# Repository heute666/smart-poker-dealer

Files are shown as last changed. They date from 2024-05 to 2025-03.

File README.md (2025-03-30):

# smart-poker-dealer
20250330: V2.4 BOM updated, to add details of "cardout sensor", stepper ISR improvement for more stable performance when weight load is high;
20250202: V2.3 BOM updated, to add comment and mistake correction;
20241114: V2 BOM updated; stepper gear (10 teeth) stp uploaded in "stl" folder - for custom design change acc. to different stepper shaft;

20241017: V2 is releasing - an emotional bot with more stable performance
3dprint files and schematic are up to date, code is under debuging and adding setup save, quick resume previous mode function
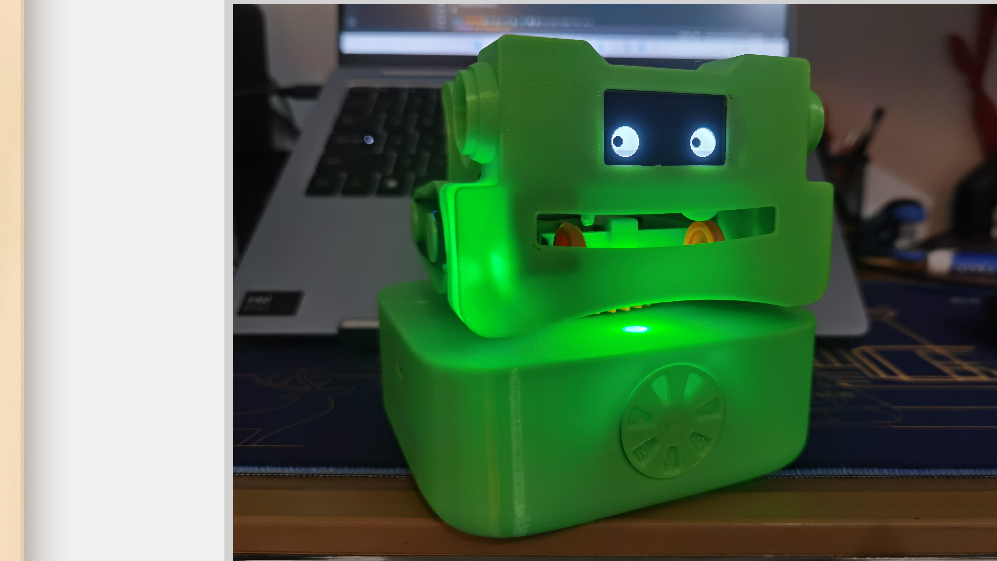
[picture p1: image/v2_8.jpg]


Initial release:
quick, light, shuffler free
3D print parts in https://www.thingiverse.com/thing:6706540;

v2 3D print, PCB updated for 1.3inch OLED, type-c charger;
PCB original files in https://oshwhub.com/heute666/pksd_indu2;

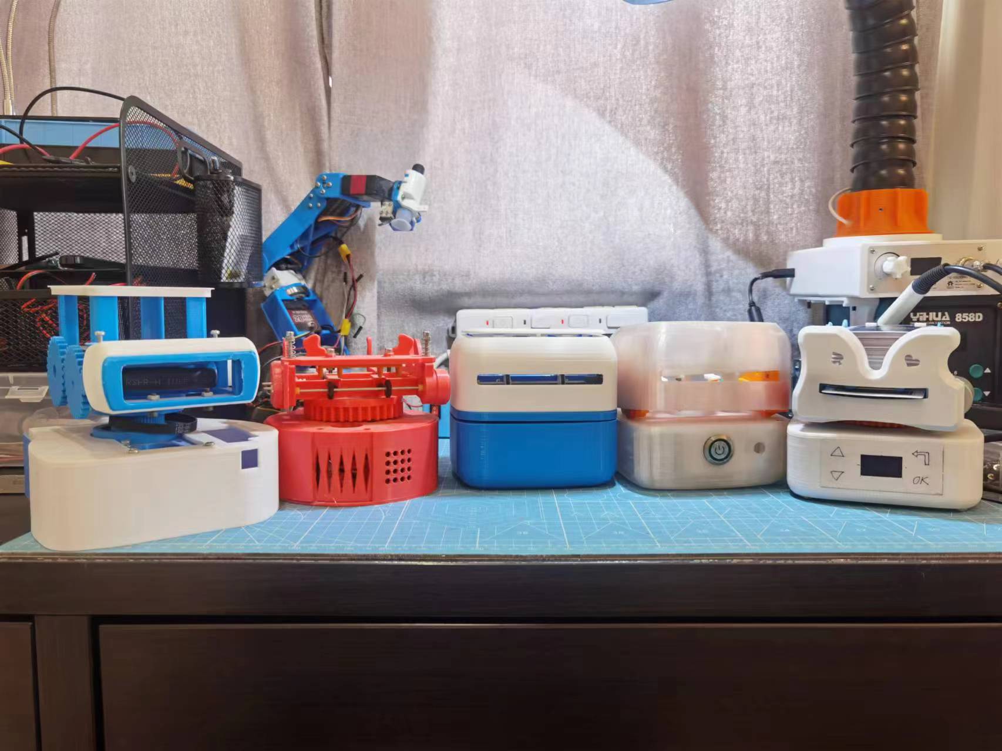
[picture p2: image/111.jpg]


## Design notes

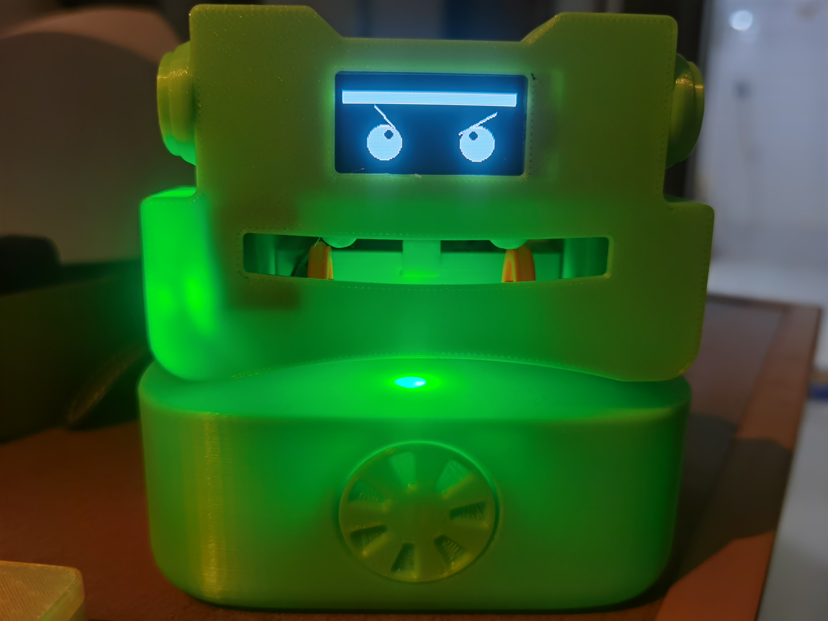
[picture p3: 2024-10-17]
image/v2_7.jpg

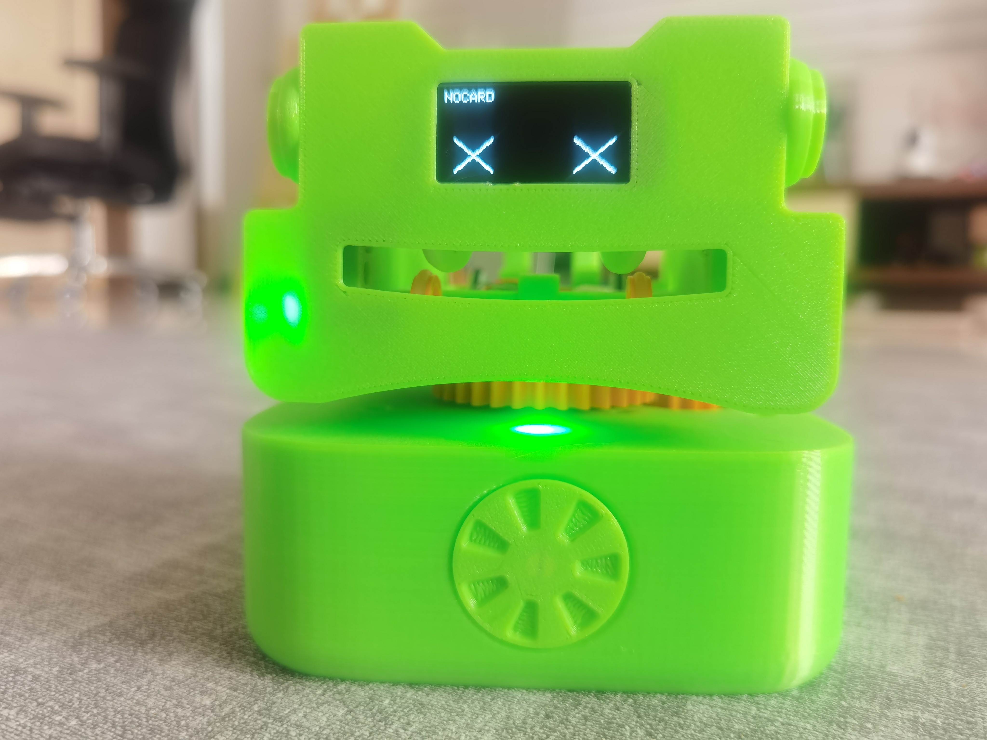
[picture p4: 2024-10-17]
image/v2_9.jpg

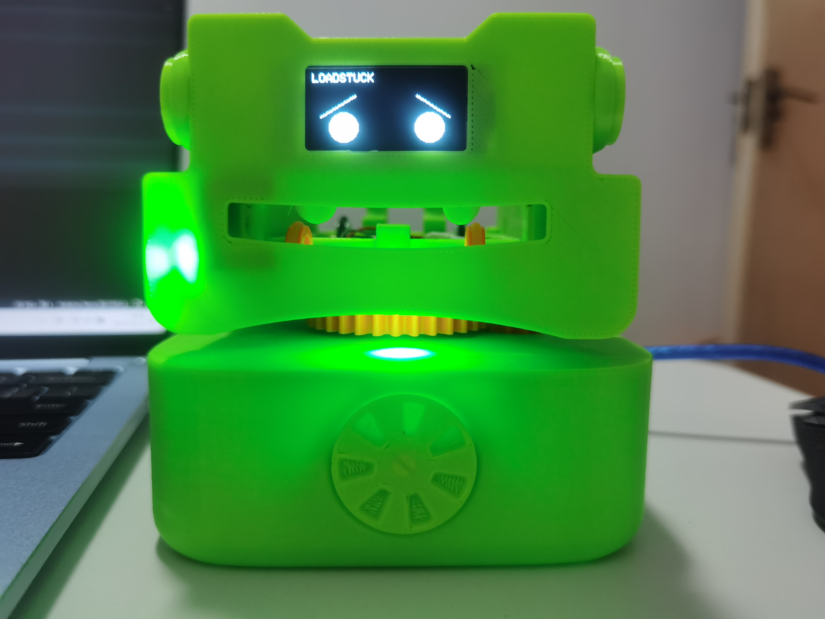
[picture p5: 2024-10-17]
image/v2_6.jpg

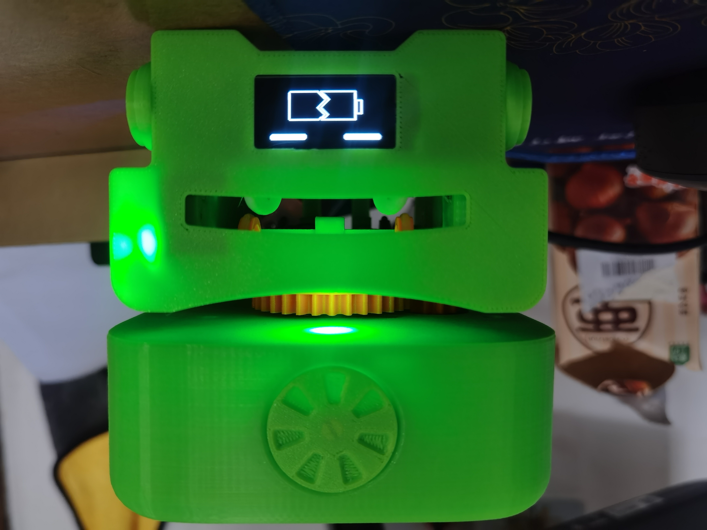
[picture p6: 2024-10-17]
image/v2_3.jpg

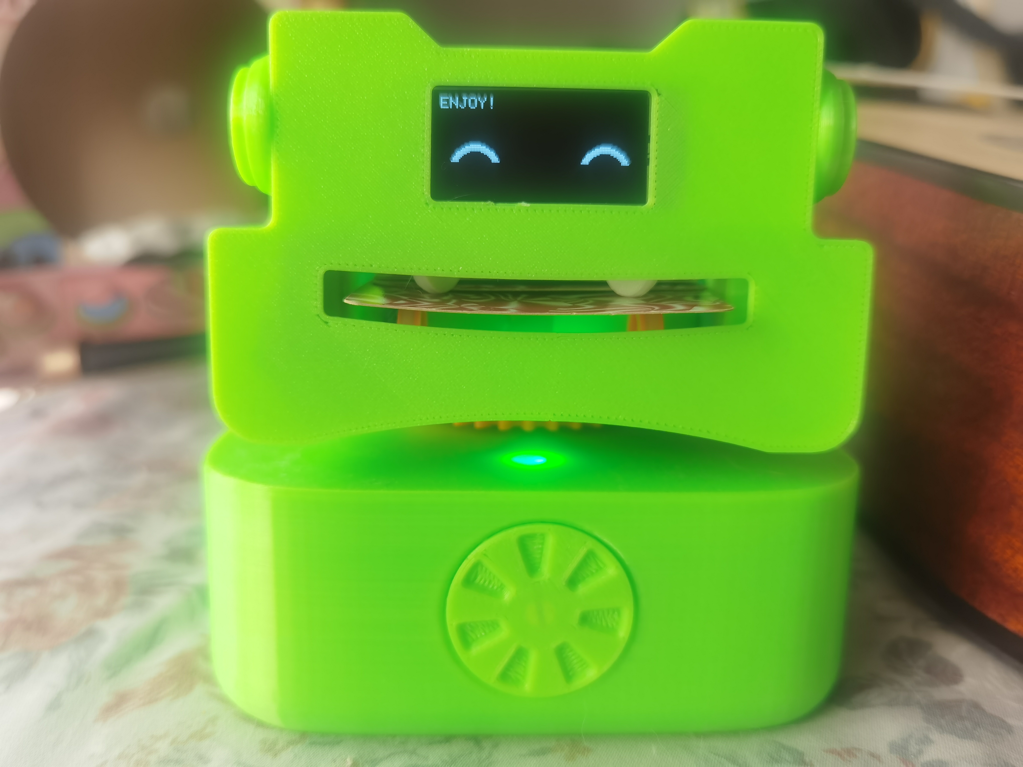
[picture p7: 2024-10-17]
image/v2_2.jpg

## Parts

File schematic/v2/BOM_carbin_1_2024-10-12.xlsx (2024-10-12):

No. | Quantity | Comment | Designator | Footprint | Value
1 | 2 | 100nf | C1,C3 | C0805 | 100nf
2 | 1 | 100uF | C2 | CAP-SMD_BD6.3-L6.6-W6.6-LS7.2-FD | 100uF
3 | 1 | NCD0805R1 | LED1 | LED0805-R-RD
4 | 1 | 330R-ori100R | R1 | R0805 | 330R-ori100R
5 | 3 | 10k | R2,R4,R5 | R0805 | 10k
6 | 1 | 20k | R3 | R0805 | 20k
7 | 1 | 1k | R6 | R0805 | 1k
8 | 1 | LM393ADR | U2 | SOIC-8_L5.0-W4.0-P1.27-LS6.0-BL
9 | 1 | ZX-PH2.0-WZ3P | U3 | CONN-TH_3P-P2.00_ZX-PH2.0-WZ3P
10 | 1 | ZX-PHB2.0-2-3PWZ | U5 | CONN-TH_6P-P2.00_ZX-PHB2.0-2-3PWZ
11 | 1 | TCRT5000 | U6 | OPTO-TH_TCRT5000
12 | 1 | WAFER-PH2.0-4PWZ | U7 | CONN-TH_4P-P2.00_WAFER-HY2.0-4PWZ

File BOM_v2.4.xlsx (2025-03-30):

 |  |  |  | https://github.com/heute666/smart-poker-dealer
L0 | L1 | L2 | L3 | L4 | 规格 | 要求 | 参考- 淘宝链接为了让大家直观知道是什么，除了备注过的，默认不代表推荐或测试过该链接实物 | 数量 | 单价 | 合计
Smart-poker-dealer |  |  |  |  |  |  |  |  |  | 135.75
 | 旋转组件
 |  | 马达侧牌仓
 |  |  | 马达侧牌仓 |  | PLA | 10齿版本- 12g 25%填充率 |  | 1 | 1.2 | 1.2
 |  |  | 直流电机总成
 |  |  |  | 直流电机 | 370 | 12V,8000-12000rpm | 淘宝链接 - 我实物是用的这种- 但超压长期运行有点容易烧 (https://item.taobao.com/item.htm?priceTId=213e36da17252054671606016e37ba&id=714138719104&ns=1&abbucket=10) | 1 | 4 | 4
 |  |  |  | 蜗杆 | 0.5M | 6-8mm长2A | 淘宝链接 (https://item.taobao.com/item.htm?id=25764808230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) | 1 | 0.08 | 0.08
 |  |  |  | 端子线 |  | PH2.0 50mm | 淘宝链接- 这里用母端 (https://item.taobao.com/item.htm?id=718353303185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) | 1 | 0.1 | 0.1
 |  |  |  | 瓷片电容 | 104 |  | 淘宝链接 (https://item.taobao.com/item.htm?priceTId=213e36da17252053488486619e37ba&id=522574858409&ns=1&abbucket=10) | 1 | 0.01 | 0.01
 |  |  | 前滚轮总成
 |  |  |  | 钢轴 | 2mm x96 | 最好95-96不会突出边界；需要用钢的，不要铁的，45或者不锈钢都行 | 淘宝链接 - 找能订做长度和倒角去毛刺的 (https://item.taobao.com/item.htm?id=563478167008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) | 1 | 0.3 | 0.3
 |  |  |  | 齿轮 | 0.5M | 10齿2A（紧配2mm轴）- 最后测下来还是10齿稳定点，需要配合10齿版本侧板用 | 淘宝链接 (https://item.taobao.com/item.htm?id=25771916651) | 1 | 0.1 | 0.1
 |  |  |  | 皮带轮 | 13mm2A |  | 淘宝链接 (https://item.taobao.com/item.htm?id=40196610656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) | 2 | 0.1 | 0.2
 |  |  |  | 硅胶圈 | 10 x 2.65 |  | 搜硅胶O型圈找对应规格 | 2 | 0.05 | 0.1
 |  |  |  | 铜轴承 | 2x4mm |  | 淘宝链接 (https://item.taobao.com/item.htm?id=534366927097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) | 2 | 0.05 | 0.1
 |  |  |  | 塑胶轴套 | 2x6mm |  | 淘宝链接 (https://item.taobao.com/item.htm?id=25735796690) | 2 | 0.02 | 0.04
 |  |  | 隔音罩 |  | TPU | 选装 |  | 1 | 0.1 | 0.1
 |  | 中间体总成
 |  |  | 牌仓传感器总成 |  |  | 可以用一个循迹传感器+特殊接线代替 |  | 1 | 2 | 2
 |  |  | 中间体 |  | PLA | 21g 25%填充率 |  | 1 | 2.1 | 2.1
 |  |  | 主轴齿轮总成
 |  |  |  | 主轴齿轮 | PLA | 12g 25%填充率 |  | 1 | 1.2 | 1.2
 |  |  |  | 螺母 | M3 |  |  | 6 | 0.02 | 0.12
 |  |  | 铜轴承 |  | 2x4mm |  | 淘宝链接 (https://item.taobao.com/item.htm?id=534366927097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) | 1 | 0.05 | 0.05
 |  |  | 螺栓 |  | M3x12 | 安装牌仓传感器 |  | 1 | 0.05 | 0.05
 |  |  | 螺栓 |  | M3x10 | 中间体连接主轴齿轮 |  | 2 | 0.05 | 0.1
 |  |  | 螺栓 |  | M2x8沉头 |  |  | 1 | 0.02 | 0.02
 |  |  | 螺母 |  | M2 |  |  | 1 | 0.02 | 0.02
 |  |  | 螺母 |  | M3 |  |  | 5 | 0.02 | 0.1
 |  | 螺栓 |  |  | M3x10 |  |  | 2 | 0.05 | 0.1
 |  | 螺母 |  |  | M3 |  |  | 2 | 0.02 | 0.04
 |  | 齿轮侧总成
 |  |  | 齿轮侧牌仓
 |  |  |  | 齿轮侧牌仓 | PLA | 15g 25%填充率 |  | 1 | 1.5 | 1.5
 |  |  |  | 螺母 | M3 |  |  | 2 | 0.02 | 0.04
 |  |  |  | 螺栓 | M2x10 |  |  | 1 | 0.02 | 0.02
 |  |  |  | 螺母 | M2 |  |  | 1 | 0.04 | 0.04
 |  |  |  | 出牌传感器总成 |  | 安装位置重要，需要PCB打板 |  | 1 | 2 | 2
 |  |  | 铜轴承 |  | 2x4mm | 几个地方需要装铜衬套当轴承的别搞错了，市面常见有2x4和2x5两种 |  | 2 | 0.05 | 0.1
 |  |  | 后滚轮总成
 |  |  |  | 同步轮 | PLA | 4g 25%填充率 |  | 4 | 0.2 | 0.8
 |  |  |  | 同步带 | MXL | 5mm宽，64齿，B64MXL |  | 1 | 0.92 | 0.92
 |  |  |  | 塑胶止挡 | 2x6mm |  |  | 1 | 0.02 | 0.02
 |  |  |  | 钢轴 | 2mm x78 | 目视无弯曲，圆柱度大约0.2？ |  | 1 | 0.3 | 0.3
 |  |  |  | 齿轮 | 0.5M | 56齿+10齿 2B |  | 1 | 0.15 | 0.15
 |  |  |  | 皮带轮 | 16mm2A |  | 淘宝链接 (https://item.taobao.com/item.htm?id=40196610656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) | 2 | 0.1 | 0.2
 |  |  |  | 氟橡胶圈 | 8.5 x 2.65 |  | 搜氟橡胶O型圈找对应规格 | 2 | 0.02 | 0.04
 |  |  | 惰齿轮
 |  |  |  | 同步轮 | PLA | 4g 25%填充率 |  | 4 | 0.2 | 0.8
 |  |  |  | 塑胶轴套 | 2x6mm |  | 淘宝链接 (https://item.taobao.com/item.htm?id=25735796690) | 1 | 0.02 | 0.02
 |  |  |  | 惰齿轮 | 0.5M | 48齿2B（单双层都可以） | 淘宝链接 (https://item.taobao.com/item.htm?id=25814212067) | 1 | 0.14 | 0.14
 |  |  |  | 惰齿轮轴 | 2mm x 10 |  | 淘宝链接 (https://item.taobao.com/item.htm?abbucket=10&id=564061088246&ns=1&priceTId=2147bf5317254444201387273e3324) | 1 | 0.04 | 0.04
 |  |  | 出牌传感器总成 |  | 如右图
 |  |  |  | PCB |  | 立创PCB文件
 |  |  |  | 电阻 | 1kΩ | 0805 |  | 1
 |  |  |  | 电阻 | 180Ω | 0805 |  | 1
 |  |  |  | 电容 | 100nf | 0805 |  | 1
 |  |  |  | LED | 自己喜欢的颜色 | 0805 |  | 1
 |  |  |  | 红外对射光耦 |  | H2010，槽宽10mm |  | 1
 |  |  |  | IC施密特发生器 |  | SN74LVC1G14DBVR SOT-23-5 |  | 1
 |  |  | 隔音罩 |  | TPU | 选装 |  | 1 | 0.1 | 0.1
 |  | 牌仓传感器PCBA |  |  |  | 制板文件和BOM，细节参阅嘉立创 | https://oshwhub.com/heute666/yi-zhi-fa-pai-ji-v1-2?code=AC-31fde32b48924dc4893be1ffcc96a859#5
 |  | 齿轮 |  |  | 0.5M | 10齿2A | 淘宝链接 (https://item.taobao.com/item.htm?id=25771916651) | 1 | 0.1 | 0.1
 |  | 铜轴承 |  |  | 2x4mm |  | 淘宝链接 (https://item.taobao.com/item.htm?id=534366927097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) | 1 | 0.05 | 0.05
 |  | 螺栓 |  |  | M3x10 |  |  | 2 | 0.05 | 0.1
 |  | 前牌仓总成
 |  |  | 出牌挡板 |  | PLA | 1g 25%填充率 |  | 2 | 0.2 | 0.4
 |  |  | 两侧装饰板 |  | PLA | 1g 25%填充率 |  | 2 | 0.2 | 0.4
 |  |  | 前牌仓 |  | PLA | 17g 25%填充率 |  | 1 | 1.7 | 1.7
 |  |  | OLED |  | 1.3寸OLED | 竖屏，SH1107驱动 |  | 1 | 13 | 13
 |  |  | 螺栓 |  | M3x8 |  |  | 2 | 0.05 | 0.1
 |  |  | 螺母 |  | M3 |  |  | 2 | 0.02 | 0.04
 |  | 后挡板 |  |  | PLA | 2g 25%填充率 |  | 2 | 0.4 | 0.8
 |  | 螺栓 |  |  | M3x8 |  |  | 2 | 0.05 | 0.1
 |  | 装饰板 |  |  | PLA | 4g 25%填充率 |  | 1 | 0.4 | 0.4
 | 底座组件
 |  | 底座总成_OP2
 |  |  | 底座总成_OP1
 |  |  |  | 轴承 | 6805 | 25mm内径，37mm外径，高7 | 淘宝链接 (https://item.taobao.com/item.htm?id=520059144981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) | 1 | 2 | 2
 |  |  |  | 底座 | PLA | 82g |  | 82 | 0.2 | 16.4
 |  |  |  | 螺母 | M3 |  |  | 2 | 0.02 | 0.04
 |  |  |  | 防滑垫 |  | 硅胶垫直径8mm-10mm都行，厚度1-2mm |  | 4 | 0.05 | 0.2
 |  |  |  | 编码器支架 | PLA | 3g |  | 3 | 0.2 | 0.6
 |  |  |  | 编码器 |  | EC11, 花轴，轴长15，5脚 |  | 1 | 1.5 | 1.5
 |  |  |  | 旋转按钮 | PLA | 3g |  | 3 | 0.2 | 0.6
 |  |  | 步进电机总成
 |  |  |  | 步进电机 | 42-34 | 常规力矩，5mm直径, 13mm长 D字短轴；短轴的不太好找，一般都是20-25mm, 太长了 | 美培亚有些二手电机轴在13-15mm之间，搜“42步进 美培亚 高34”会有些，轴径3-5的圆轴D轴都有，得改图，我把STEP放上来 | 1 | 15 | 15
 |  |  |  | 步进电机齿轮 | PLA | 1M10T, 2g |  | 1 | 0.2 | 0.2
 |  |  |  | 连接端子线 |  | PH2.0 6pin + 24AWG +XH2.54 4pin |  | 1 | 0.1 | 0.1
 |  |  | 螺栓 |  | M3X10 | 沉头，带减震垫用，固定步进电机 |  | 4 | 0.05 | 0.2
 |  |  | 螺栓 |  | M3X8 | 沉头，不带减震垫用，固定步进电机 |  | 4 |  | 0
 |  |  | 主控PCB总成
 |  |  |  | 主控PCB |  | 立创上是配v2壳体的版本 | https://u.lceda.cn/account/user/projects/index/detail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 | 1 | 15 | 15
 |  |  |  | 步进电机驱动 | TMC2208 | 也可用TMC2225 |  | 1 | 10 | 10
 | v1 |  | 屏幕及触摸模块
 | v1 |  |  | OLED屏 | 0.96 I2C | 配V1壳 |  | 1 | 10
 | v1 |  |  | OLED屏 | 1.3 I2C | 配V2壳
 | v1 |  |  | 触摸模块PCB |  | 立创上是配v2壳体的版本 | https://u.lceda.cn/account/user/projects/index/detail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 | 1 | 4
 | v1 |  |  | 端子线 |  | X2.54 8pin |  | 1 | 0.2
 | v1 |  |  | 热熔胶
 | v1 |  |  | 导电胶带 |  | 可靠性不好，将改成导电线直接埋进外壳
 | v1 |  | 铜柱 |  |  | M3, 10mm高，一边公一边母 |  | 2 | 0.3
 |  |  | 导电环支架 | v2 | PLA | 7g |  | 7 | 0.2 | 1.4
 |  |  | 电池盒 |  |  | 18650，2节串联 |  | 1 | 1 | 1
 |  |  | 螺栓 |  | M3X8 | 沉头，固定导电环支架和电池盒 |  | 5 | 0.05 | 0.25
 |  |  | 螺母 |  | M3 | 固定导电环支架和电池盒 |  | 5 | 0.02 | 0.1
 | 导电环 |  |  |  | 2A8路 | 尺寸不超过22mm直径26高,可多几路，要求并不高，咸鱼上的就可以 | 以前挺多库存件几块钱的，现在好难找，这家12路2A，塑料22mm直径，19mm长的应该可以，30块 (https://detail.tmall.com/item.htm?id=559037397190&skuId=3646480359811) | 1 | 20 | 20
 | 主轴齿轮固定片 |  |  |  | PLA | 3g |  | 1 | 0.3 | 0.3
 | 螺栓 |  |  |  | M3x8 | 固定主轴齿轮 |  | 3 | 0.05 | 0.15
 | 螺母 |  |  |  | M3 | 固定主轴齿轮 |  | 3 | 0.02 | 0.06
 | 电池 |  |  |  | 18650 | 1600mA-2000mA的就可以，动力电池更好，5C |  | 2 | 7 | 14

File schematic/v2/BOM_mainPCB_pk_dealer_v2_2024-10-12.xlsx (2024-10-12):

No. | Quantity | Comment | Designator | Footprint | Value
1 | 1 | 0.22uf | C1 | C0805
2 | 3 | 100uF | C2,C3,C39 | CAP-SMD_BD6.3-L6.6-W6.6-FD | 100uF
3 | 1 | 0.1uf | C4 | C0805
4 | 6 | 22uf | C5,C7,C27,C28,C33,C34 | C0805
5 | 3 | 100n | C6,C15,C16 | C0805
6 | 1 | 220uF | C14 | CAP-TH_BD8.0-P3.50-D0.6-FD | 220uF
7 | 1 | 4.7uF | C17 | CAP-SMD_L3.2-W1.6-FD | 4.7uF
8 | 2 | 22p | C25,C26 | C0805
9 | 4 | 10uf | C29,C31,C35,C36 | C0805
10 | 3 | 100nf | C30,C37,C38 | C0805
11 | 2 | SS54A | D2,D3 | SMA_L4.2-W2.6-LS5.1-RD
12 | 1 | MM1Z5V1 | D7 | SOD-123_L2.7-W1.6-LS3.7-RD
13 | 1 | SS54 | D8 | SMA_L4.3-W2.6-LS5.0-FD
14 | 1 | ICSP-6 | ISP | ICSP-6
15 | 1 | HC-PHD-2*3AW | J1 | CONN-TH_6P-P2.00_HCTL_HC-PHD
16 | 1 | HC-PHD-2*3A | J2 | CONN-TH_6P-P2.00_HCTL_HC-PHD-2X3A
17 | 2 | 4.7uH | L1,L2 | IND-SMD_L7.0-W6.6_0630CDMCCDS
18 | 1 | 2.2uH | L3 | IND-SMD_L7.0-W6.6_0630CDMCCDS
19 | 1 | 0.25R | R1 | R0805
20 | 1 | 100kΩ | R2 | RES-ADJ-SMD_VG039NCH
21 | 4 | 100K | R3,R4,R7,R8 | R0805
22 | 3 | 10K | R5,R6,R13 | R0805
23 | 3 | 1K | R9,R18,R29 | R0805
24 | 2 | optional | R12,R16 | R0402 | optional
25 | 2 | 51K | R17,R20 | R0805
26 | 1 | 75K | R19 | R0805
27 | 1 | 0.5R | R21 | R0805
28 | 3 | 5.1k | R22,R30,R31 | R0805
29 | 1 | 100R | R23 | R1206
30 | 1 | TMC2208模块 | U2 | TMC2208
31 | 1 | XH2.54-LI-4P | U3 | CONN-TH_4P-P2.54-XH2.54-LI-4P
32 | 2 | SX1308 | U4,U5 | SOT-23-6_L2.9-W1.6-P0.95-LS2.8-BR
33 | 1 | BLE | U6 | HDR-TH_4P-P2.54-V-M
34 | 1 | DRV8870DDA | U7 | SOPOWERPAD-8_L4.9-W3.9-P1.27-LS6.0-BL-EP
35 | 1 | ATMEGA328P-AU | U8 | TQFP-32_L7.0-W7.0-P0.80-LS9.0-BL
36 | 1 | XH2.54-LI-2P_C2922484 | U13 | CONN-TH_XH-2AW_C2908611
37 | 1 | AMS1117-5.0 | U17 | SOT-223_L6.7-W3.5-P2.30-BR
38 | 1 | IP2326 | U18 | VQFN-24_L4.0-W4.0-P0.50-BL-EP2.5
39 | 1 | BAT_CON | U19 | CONN-TH_3P-P2.54_2501S-3P
40 | 1 | SWI | U20 | SW-TH_SHOU-HAN_SS12D10G4
41 | 1 | TJ-L5FPTXHMCSLCRGB-A5 | U22 | LED-TH_4P-BD5.8-P1.30
42 | 1 | TYPE-C16PIN | USB6 | USB-C-SMD_TYPE-C16PIN
43 | 1 | 16MHz | X2 | QS

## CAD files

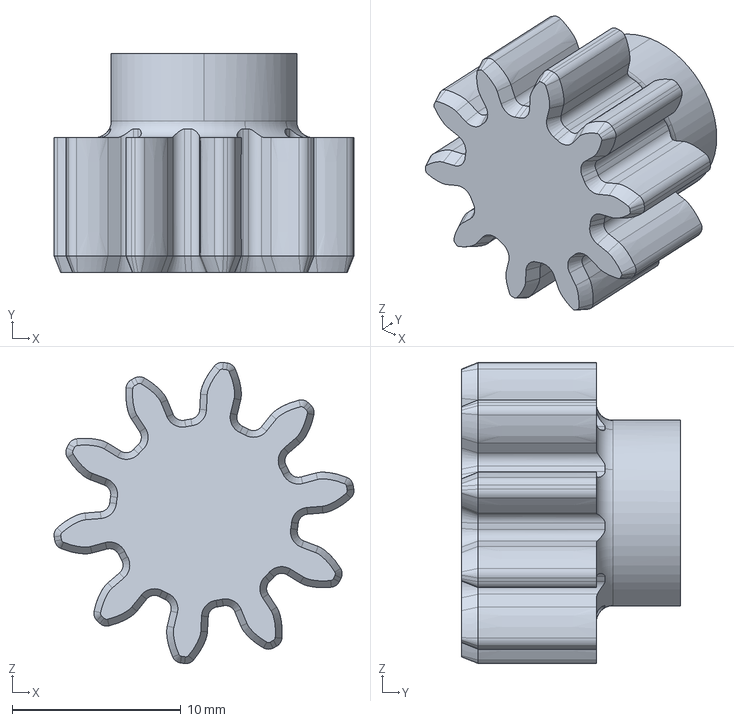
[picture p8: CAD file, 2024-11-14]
3dprint/gear_10t.stp
17.8 x 13.0 x 17.9 mm

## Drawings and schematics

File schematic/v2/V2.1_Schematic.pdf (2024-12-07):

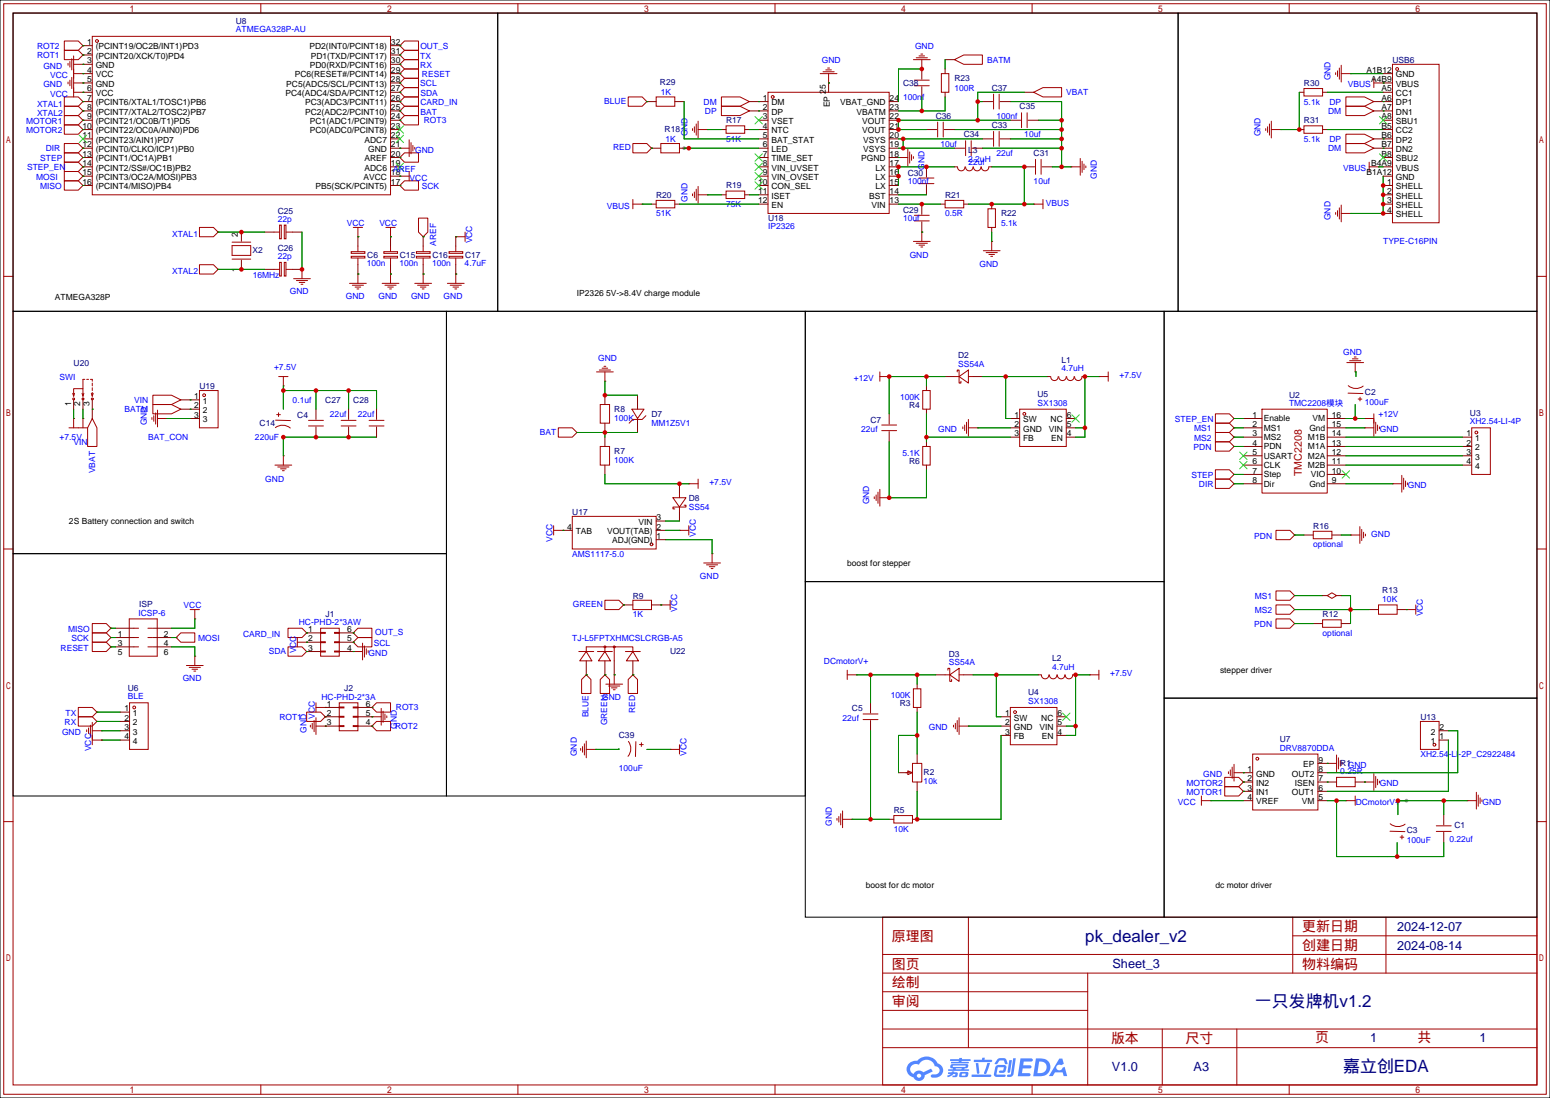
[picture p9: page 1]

C33
C34 | 10uf
10uf

2S Battery connection and switch

boost for dc motor

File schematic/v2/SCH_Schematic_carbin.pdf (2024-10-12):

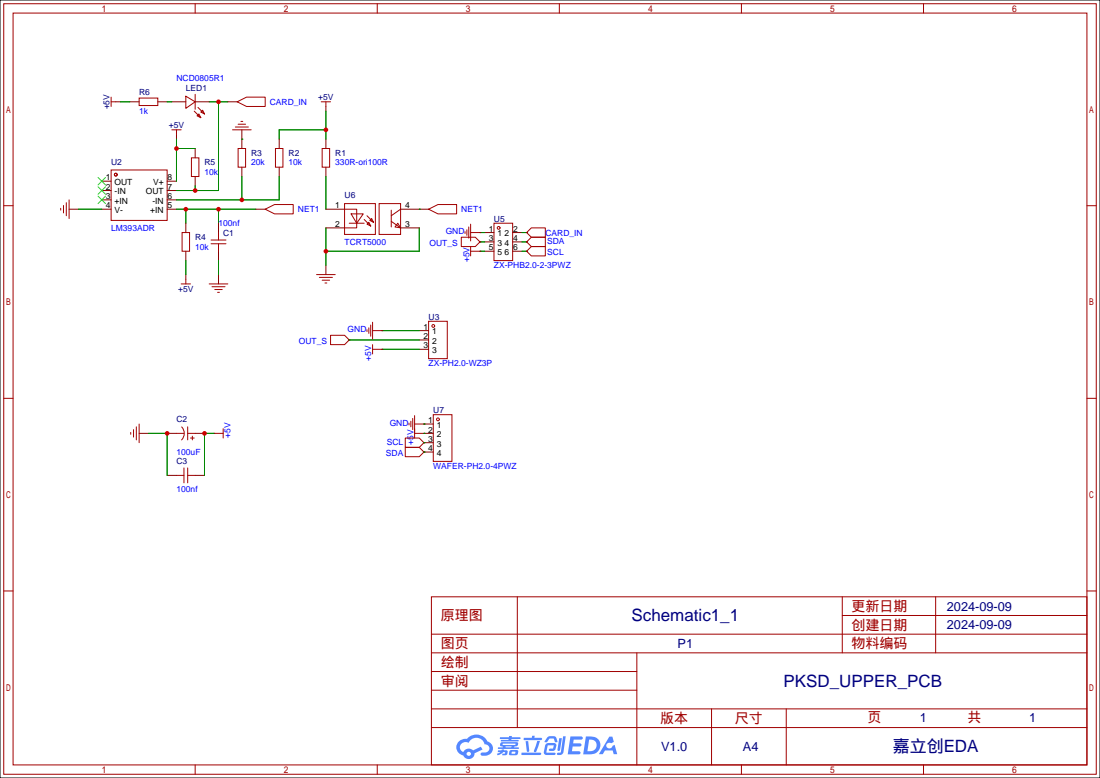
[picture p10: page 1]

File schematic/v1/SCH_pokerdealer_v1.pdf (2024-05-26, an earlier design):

# Your Company TMC²²⁰⁸

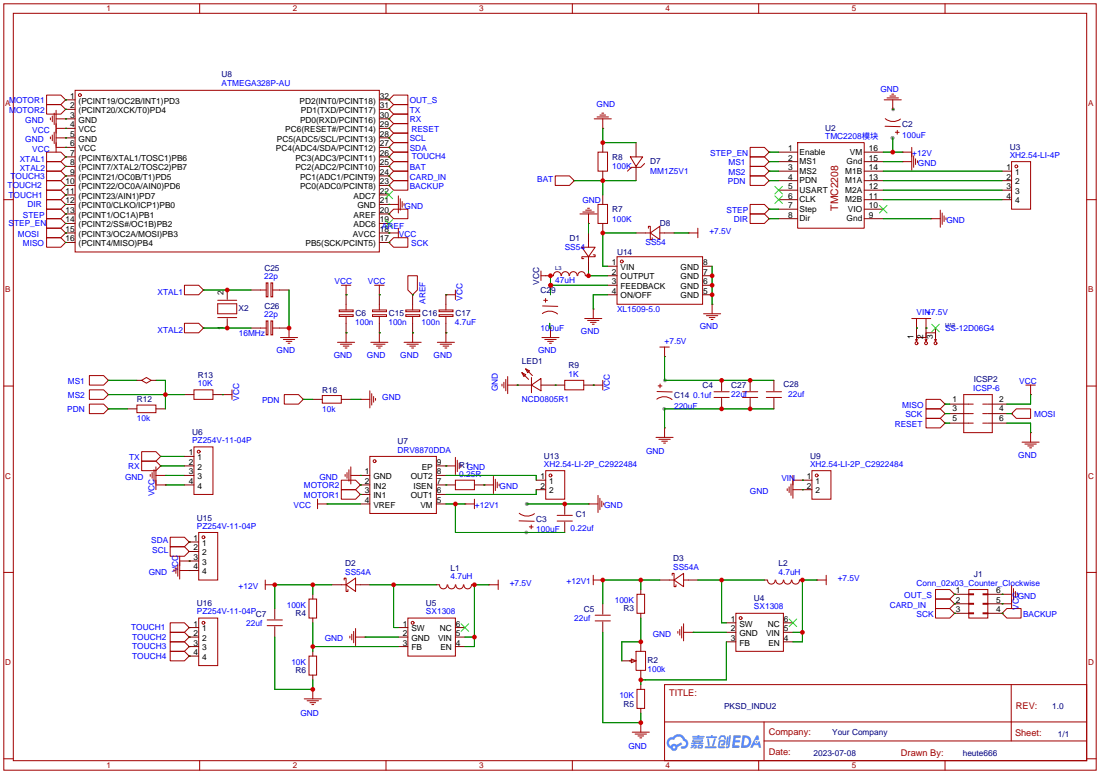
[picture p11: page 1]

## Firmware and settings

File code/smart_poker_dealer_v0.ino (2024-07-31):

#include <Adafruit_SSD1306.h>
//#include <Adafruit_SH110X.h>
//#include <EEPROM.h>
#define screen_enable
//#define ble_enable
//#define record_time
#ifdef screen_enable
#define SCREEN_ADDRESS 0x3C                    ///< See datasheet for Address; 0x3D for 128x64, 0x3C for 128x32
Adafruit_SSD1306 display(128, 64, &Wire, -1);  // I2C / TWI
//Adafruit_SH1106G display = Adafruit_SH1106G(128, 64, &Wire, -1);
const unsigned char PROGMEM str_guandan[] ={0x00,0x00,0x00,0x00,0x00,0x00,0x00,0x00,0x00,0x00,0x00,0x00,0x7C,0x00,0x00,0x00,0x01,0xFF,0x00,0x00,0x00,0x03,0x78,0xC0,0x00,0x00,0x0C,0xAF,0x20,0x00,0x00,0x1F,
0xDF,0xF0,0x00,0x00,0x3F,0xFF,0xF8,0x00,0x00,0x7F,0xFF,0xFC,0x00,0x00,0x7F,0xFF,0xFC,0x00,0x00,0xFD,0xFF,0xBE,0x00,0x00,0xFF,0xEF,0xFE,0x00,0x00,0xFF,0xC7,0xFE,
0x20,0x00,0xFF,0x83,0xFE,0x30,0x08,0xCF,0xC7,0x9F,0x78,0x0C,0xB7,0xEF,0x6F,0x78,0x1C,0x7B,0x86,0xE7,0xFC,0x1E,0x7F,0xB9,0xFB,0x7C,0x3F,0xFD,0x7F,0xFC,0xFC,0x3F,
0xFE,0x7F,0xFF,0xFC,0x3F,0xFF,0xFF,0xFF,0xFC,0x3F,0xFF,0xFF,0xFF,0xFC,0x3F,0xFF,0xFF,0xFF,0xFC,0x3F,0xFF,0xFF,0xFF,0xF8,0x1F,0xFF,0xFF,0xFF,0xF8,0x1F,0xFF,0xFF,
0xFF,0xF0,0x0F,0xFF,0xFF,0xFF,0xF0,0x0F,0xFF,0xFF,0xFF,0xE0,0x07,0xFF,0xFF,0xFF,0xE0,0x07,0xFF,0xFF,0xFF,0xC0,0x03,0xFF,0xFF,0xFF,0xC0,0x03,0xFF,0xFF,0xFF,0x80,
0x01,0xFF,0xFF,0xFF,0x00,0x00,0xFF,0xFF,0xFF,0x00,0x00,0x7F,0xFF,0xFC,0x00,0x00,0x1F,0xFF,0xF8,0x00,0x00,0x0F,0xFF,0xE0,0x00,0x00,0x01,0xFF,0x00,0x00,0x00,0x00,
0x00,0x00,0x00,0x00,0x00,0x00,0x00,0x00}; //40x40
static const unsigned char PROGMEM str_doudizhu[] ={0x00,0x00,0x00,0x00,0x00,0x00,0x00,0x3C,0x00,0x00,0x00,0x03,0xFF,0xC0,0x00,0x00,0x1F,0xFF,0xF8,0x00,0x00,0x3F,0x81,0xFC,0x00,0x00,0xFC,0x00,0x3F,0x00,0x01,0xF0,
0x00,0x0F,0x80,0x03,0xE0,0x02,0x07,0xC0,0x07,0xC0,0x03,0x03,0xE0,0x0F,0x80,0x03,0x01,0xF0,0x0F,0x00,0xF3,0x00,0xF0,0x1F,0x00,0x73,0x00,0xF8,0x1E,0x00,0x63,0x00,
0x78,0x3E,0x00,0x83,0x00,0x7C,0x3E,0x01,0xE3,0x00,0x7C,0x3C,0x00,0xF3,0x70,0x3C,0x3C,0x00,0xC7,0xF0,0x3E,0x7C,0x01,0xBF,0x00,0x3E,0x7C,0x00,0x73,0x00,0x3E,0x7C,
0x01,0xC3,0x00,0x3E,0x7C,0x07,0x03,0x00,0x3E,0x7E,0x1E,0x03,0x00,0x7E,0x7E,0x1C,0x03,0x00,0x7E,0x7E,0x00,0x03,0x00,0x7E,0x3F,0x00,0x03,0x00,0xFC,0x3F,0x00,0x03,
0x00,0xFC,0x3F,0x80,0x03,0x01,0xFC,0x3F,0xC0,0x03,0x03,0xFC,0x3F,0xE0,0x02,0x07,0xFC,0x1F,0xF0,0x00,0x0F,0xF8,0x1F,0xFC,0x00,0x3F,0xF8,0x0F,0xFF,0x81,0xFF,0xF0,
0x07,0xFF,0xFF,0xFF,0xE0,0x07,0xFF,0xFF,0xFF,0xE0,0x03,0xFF,0xFF,0xFF,0xC0,0x00,0xFF,0xFF,0xFF,0x00,0x00,0x3F,0xFF,0xFC,0x00,0x00,0x0F,0xFF,0xF0,0x00,0x00,0x03,
0xFF,0xC0,0x00,0x00,0x00,0x00,0x00,0x00};
static const unsigned char PROGMEM str_tao[] ={0x00,0x00,0x3C,0x00,0x00,0x00,0x00,0x7E,0x00,0x00,0x00,0x00,0xFF,0x00,0x00,0x00,0x01,0xFF,0x80,0x00,0x00,0x03,0xFF,0xC0,0x00,0x00,0x07,0xFF,0xE0,0x00,0x00,0x0F,
0xFF,0xF0,0x00,0x00,0x1F,0xFF,0xF8,0x00,0x00,0x3F,0xFF,0xFC,0x00,0x00,0x7F,0xFF,0xFE,0x00,0x00,0xFF,0xFF,0xFF,0x00,0x01,0xFF,0xFF,0xFF,0x80,0x03,0xFF,0xFF,0xFF,
0xC0,0x07,0xFF,0xFF,0xFF,0xE0,0x0F,0xFF,0xFF,0xFF,0xF0,0x1F,0xFF,0xFF,0xFF,0xF0,0x1F,0xFF,0xFF,0xFF,0xF8,0x3F,0xFF,0xFF,0xFF,0xFC,0x3F,0xFF,0xFF,0xFF,0xFC,0x7F,
0xFF,0xFF,0xFF,0xFE,0x7F,0xFF,0xFF,0xFF,0xFE,0x7F,0xFF,0xFF,0xFF,0xFE,0x7F,0xFF,0xFF,0xFF,0xFE,0x7F,0xFF,0xFF,0xFF,0xFE,0x7F,0xFF,0xFF,0xFF,0xFE,0x3F,0xFF,0xFF,
0xFF,0xFC,0x3F,0xFF,0xFF,0xFF,0xFC,0x1F,0xFF,0xFF,0xFF,0xF8,0x0F,0xFF,0xFF,0xFF,0xF0,0x0F,0xFF,0xFF,0xFF,0xF0,0x07,0xFF,0xFF,0xFF,0xE0,0x01,0xFF,0x7E,0xFF,0x80,
0x00,0xFC,0x7E,0x7E,0x00,0x00,0x00,0xFF,0x00,0x00,0x00,0x00,0xFF,0x00,0x00,0x00,0x01,0xFF,0x80,0x00,0x00,0x01,0xFF,0x80,0x00,0x00,0x03,0xFF,0xC0,0x00,0x00,0x03,
0xFF,0xC0,0x00,0x00,0x07,0xFF,0xE0,0x00};
const unsigned char PROGMEM str_xin[] ={0x00,0x00,0x00,0x00,0x00,0x01,0xF8,0x00,0x0F,0x80,0x07,0xFE,0x00,0x3F,0xE0,0x0F,0xFF,0x00,0x7F,0xF0,0x1F,0xFF,0x80,0xFF,0xF8,0x3F,0xFF,0xC1,0xFF,0xFC,0x7F,0xFF,
0xC1,0xFF,0x7E,0x7F,0xFF,0xE3,0xFF,0xBE,0xFF,0xFF,0xF7,0xFF,0xDF,0xFF,0xFF,0xFF,0xFF,0xEF,0xFF,0xFF,0xFF,0xFF,0xF7,0xFF,0xFF,0xFF,0xFF,0xF7,0xFF,0xFF,0xFF,0xFF,
0xF7,0xFF,0xFF,0xFF,0xFF,0xF7,0xFF,0xFF,0xFF,0xFF,0xF7,0xFF,0xFF,0xFF,0xFF,0xFF,0xFF,0xFF,0xFF,0xFF,0xFF,0xFF,0xFF,0xFF,0xFF,0xFF,0x7F,0xFF,0xFF,0xFF,0xFE,0x7F,
0xFF,0xFF,0xFF,0xFE,0x3F,0xFF,0xFF,0xFF,0xFC,0x1F,0xFF,0xFF,0xFF,0xF8,0x0F,0xFF,0xFF,0xFF,0xF0,0x07,0xFF,0xFF,0xFF,0xE0,0x03,0xFF,0xFF,0xFF,0xC0,0x01,0xFF,0xFF,
0xFF,0x80,0x00,0xFF,0xFF,0xFF,0x00,0x00,0x7F,0xFF,0xFE,0x00,0x00,0x3F,0xFF,0xFC,0x00,0x00,0x1F,0xFF,0xF8,0x00,0x00,0x0F,0xFF,0xF0,0x00,0x00,0x07,0xFF,0xE0,0x00,
0x00,0x03,0xFF,0xC0,0x00,0x00,0x01,0xFF,0x80,0x00,0x00,0x00,0xFF,0x00,0x00,0x00,0x00,0x7E,0x00,0x00,0x00,0x00,0x3C,0x00,0x00,0x00,0x00,0x18,0x00,0x00,0x00,0x00,
0x00,0x00,0x00,0x00,0x00,0x00,0x00,0x00};
static const unsigned char PROGMEM str_mei[] ={0x00,0x00,0xFF,0x00,0x00,0x00,0x03,0xFF,0xC0,0x00,0x00,0x07,0xFF,0xE0,0x00,0x00,0x0F,0xFF,0xF0,0x00,0x00,0x0F,0xFF,0xF0,0x00,0x00,0x1F,0xFF,0xF8,0x00,0x00,0x1F,
0xFF,0xFC,0x00,0x00,0x3F,0xFF,0xFC,0x00,0x00,0x3F,0xFF,0xFC,0x00,0x00,0x3F,0xFF,0xFC,0x00,0x00,0x3F,0xFF,0xFC,0x00,0x00,0x3F,0xFF,0xFC,0x00,0x00,0x1F,0xFF,0xF8,
0x00,0x00,0x1F,0xFF,0xF8,0x00,0x00,0x0F,0xFF,0xF0,0x00,0x00,0xE7,0xFF,0xE7,0x80,0x07,0xFB,0xFF,0xDF,0xE0,0x1F,0xFD,0xFF,0xBF,0xF8,0x3F,0xFF,0xFF,0xFF,0xF8,0x3F,
0xFF,0xFF,0xFF,0xFC,0x7F,0xFF,0xFF,0xFF,0xFE,0x7F,0xFF,0xFF,0xFF,0xFE,0xFF,0xFF,0xFF,0xFF,0xFE,0xFF,0xFF,0xFF,0xFF,0xFF,0xFF,0xFF,0xFF,0xFF,0xFF,0xFF,0xFF,0xFF,
0xFF,0xFF,0xFF,0xFF,0xFF,0xFF,0xFF,0xFF,0xFF,0xFF,0xFF,0xFE,0x7F,0xFF,0xFF,0xFF,0xFE,0x7F,0xFF,0xFF,0xFF,0xFE,0x3F,0xFF,0xFF,0xFF,0xFC,0x3F,0xFF,0xBD,0xFF,0xFC,
0x1F,0xFF,0x3C,0xFF,0xF8,0x0F,0xFE,0x3E,0x7F,0xF0,0x03,0xF8,0x7E,0x1F,0xC0,0x00,0x00,0x7E,0x00,0x00,0x00,0x00,0xFF,0x00,0x00,0x00,0x01,0xFF,0x80,0x00,0x00,0x03,
0xFF,0xC0,0x00,0x00,0x00,0x00,0x00,0x00};
const unsigned char PROGMEM str_fang[] ={0x00,0x00,0x80,0x00,0x00,0x00,0x01,0xC0,0x00,0x00,0x00,0x03,0xE0,0x00,0x00,0x00,0x07,0xF0,0x00,0x00,0x00,0x0F,0xF8,0x00,0x00,0x00,0x1F,0xFC,0x00,0x00,0x00,0x1F,
0xFE,0x00,0x00,0x00,0x3F,0xFF,0x00,0x00,0x00,0x7F,0xFF,0x80,0x00,0x00,0xFF,0xFF,0xC0,0x00,0x01,0xFF,0xFF,0xE0,0x00,0x03,0xFF,0xFF,0xF0,0x00,0x07,0xFF,0xFF,0xF0,
0x00,0x0F,0xFF,0xFF,0xF8,0x00,0x1F,0xFF,0xFF,0xFC,0x00,0x3F,0xFF,0xFF,0xFE,0x00,0x7F,0xFF,0xFF,0xFF,0x00,0x7F,0xFF,0xFF,0xFF,0x80,0xFF,0xFF,0xFF,0xFF,0x80,0xFF,
0xFF,0xFF,0xFF,0x80,0xFF,0xFF,0xFF,0xFF,0xC0,0xFF,0xFF,0xFF,0xFF,0x80,0x7F,0xFF,0xFF,0xFF,0x80,0x3F,0xFF,0xFF,0xFF,0x00,0x1F,0xFF,0xFF,0xFE,0x00,0x0F,0xFF,0xFF,
0xFC,0x00,0x07,0xFF,0xFF,0xF8,0x00,0x03,0xFF,0xFF,0xF0,0x00,0x03,0xFF,0xFF,0xE0,0x00,0x01,0xFF,0xFF,0xC0,0x00,0x00,0xFF,0xFF,0xC0,0x00,0x00,0x7F,0xFF,0x80,0x00,
0x00,0x3F,0xFF,0x00,0x00,0x00,0x1F,0xFE,0x00,0x00,0x00,0x0F,0xFC,0x00,0x00,0x00,0x07,0xF8,0x00,0x00,0x00,0x03,0xF0,0x00,0x00,0x00,0x01,0xE0,0x00,0x00,0x00,0x00,
0xC0,0x00,0x00,0x00,0x00,0x00,0x00,0x00};
const unsigned char PROGMEM str_play[] ={0x00,0x00,0x00,0x00,0x00,0x30,0x00,0x00,0x00,0x00,0x3C,0x00,0x00,0x00,0x00,0x3F,0x00,0x00,0x00,0x00,0x3F,0xC0,0x00,0x00,0x00,0x3F,0xF0,0x00,0x00,0x00,0x3F,0xFC,
0x00,0x00,0x00,0x3F,0xFF,0x00,0x00,0x00,0x3F,0xFF,0xC0,0x00,0x00,0x3F,0xFF,0xF0,0x00,0x00,0x3F,0xFF,0xFC,0x00,0x00,0x3F,0xFF,0xFF,0x00,0x00,0x3F,0xFF,0xFF,0xC0,
0x00,0x3F,0xFF,0xFF,0xF0,0x00,0x3F,0xFF,0xFF,0xFC,0x00,0x3F,0xFF,0xFF,0xFF,0x00,0x3F,0xFF,0xFF,0xFF,0xC0,0x3F,0xFF,0xFF,0xFF,0xF0,0x3F,0xFF,0xFF,0xFF,0xFC,0x3F,
0xFF,0xFF,0xFF,0xFE,0x3F,0xFF,0xFF,0xFF,0xFE,0x3F,0xFF,0xFF,0xFF,0xF8,0x3F,0xFF,0xFF,0xFF,0xE0,0x3F,0xFF,0xFF,0xFF,0x80,0x3F,0xFF,0xFF,0xFE,0x00,0x3F,0xFF,0xFF,
0xF8,0x00,0x3F,0xFF,0xFF,0xE0,0x00,0x3F,0xFF,0xFF,0x80,0x00,0x3F,0xFF,0xFE,0x00,0x00,0x3F,0xFF,0xF8,0x00,0x00,0x3F,0xFF,0xE0,0x00,0x00,0x3F,0xFF,0x80,0x00,0x00,
0x3F,0xFE,0x00,0x00,0x00,0x3F,0xF8,0x00,0x00,0x00,0x3F,0xE0,0x00,0x00,0x00,0x3F,0x80,0x00,0x00,0x00,0x3E,0x00,0x00,0x00,0x00,0x38,0x00,0x00,0x00,0x00,0x00,0x00,
0x00,0x00,0x00,0x00,0x00,0x00,0x00,0x00};
const unsigned char PROGMEM str_continue[] ={0x00,0x00,0x00,0x00,0x00,0x00,0x00,0x08,0x00,0x00,0x00,0x00,0x0C,0x00,0x00,0x00,0x00,0x0E,0x00,0x00,0x00,0x00,0x0F,0x00,0x00,0x00,0x00,0x0F,0x80,0x00,0x00,0x00,
0x0F,0xC0,0x00,0x00,0x00,0x0F,0xE0,0x00,0x00,0x00,0x0F,0xF0,0x00,0x00,0x00,0x0F,0xF8,0x00,0x5D,0xEF,0xFF,0xFC,0x00,0x5D,0xEF,0xFF,0xFE,0x00,0x5D,0xEF,0xFF,0xFF,
0x00,0x5D,0xEF,0xFF,0xFF,0x80,0x5D,0xEF,0xFF,0xFF,0xC0,0x5D,0xEF,0xFF,0xFF,0xE0,0x5D,0xEF,0xFF,0xFF,0xF0,0x5D,0xEF,0xFF,0xFF,0xF8,0x5D,0xEF,0xFF,0xFF,0xFC,0x5D,
0xEF,0xFF,0xFF,0xFE,0x5D,0xEF,0xFF,0xFF,0xFE,0x5D,0xEF,0xFF,0xFF,0xFC,0x5D,0xEF,0xFF,0xFF,0xF8,0x5D,0xEF,0xFF,0xFF,0xF0,0x5D,0xEF,0xFF,0xFF,0xE0,0x5D,0xEF,0xFF,
0xFF,0xC0,0x5D,0xEF,0xFF,0xFF,0x80,0x5D,0xEF,0xFF,0xFF,0x00,0x5D,0xEF,0xFF,0xFE,0x00,0x5D,0xEF,0xFF,0xFC,0x00,0x00,0x00,0x0F,0xF8,0x00,0x00,0x00,0x0F,0xF0,0x00,
0x00,0x00,0x0F,0xE0,0x00,0x00,0x00,0x0F,0xC0,0x00,0x00,0x00,0x0F,0x80,0x00,0x00,0x00,0x0F,0x00,0x00,0x00,0x00,0x0E,0x00,0x00,0x00,0x00,0x0C,0x00,0x00,0x00,0x00,
0x08,0x00,0x00,0x00,0x00,0x00,0x00,0x00};
const unsigned char PROGMEM str_setup[] ={0x00,0x00,0x00,0x18,0x00,0x00,0x00,0x7C,0x3E,0x00,0x00,0x00,0xFC,0x3E,0x00,0x00,0x01,0xFE,0x7E,0x00,0x00,0x01,0xFF,0xFE,0x00,0x00,0x00,0xFF,0xFE,0x00,0x00,0x00,
0xFF,0xFE,0x80,0x00,0x01,0xFE,0x3E,0xFC,0x00,0x3F,0xF0,0x0E,0xFC,0x00,0x3F,0xE7,0xE2,0xFE,0x00,0x7F,0xCF,0xFA,0xFE,0x00,0x7F,0x9F,0xFC,0xFE,0x00,0x7F,0xBF,0xFC,
0xFE,0x00,0x3F,0x3F,0xFC,0xF8,0x00,0x0F,0x3F,0xFE,0xF0,0x00,0x0F,0x3F,0xFE,0xD0,0x00,0x0F,0x3F,0xFE,0x80,0x00,0x0F,0x3F,0xFC,0xA4,0x00,0x78,0x3F,0xFC,0x76,0x00,
0x7C,0x1F,0xF9,0x7A,0x0C,0x7C,0xEF,0xF0,0xFA,0x0F,0x7D,0xF3,0xE0,0xFC,0x0F,0xFF,0xF0,0x0C,0xFC,0x0F,0xC7,0xF2,0x3C,0x00,0x07,0x03,0xE3,0xFC,0x00,0x0E,0x00,0xE3,
0xFC,0x00,0x34,0x00,0xFB,0xFF,0x80,0xF0,0x00,0x7D,0xFC,0x00,0xF8,0x00,0x7C,0x38,0x00,0xF8,0x00,0x7C,0x10,0x00,0xFC,0x00,0xFC,0x00,0x00,0x1E,0x00,0xF0,0x00,0x00,
0x0E,0x01,0xE0,0x00,0x00,0x0F,0x83,0xE0,0x00,0x00,0x1F,0x8F,0xF0,0x00,0x00,0x3F,0xE3,0xE0,0x00,0x00,0x1F,0x78,0x00,0x00,0x00,0x0C,0x7C,0x40,0x00,0x00,0x00,0x7C,
0x00,0x00,0x00,0x00,0x38,0x00,0x00,0x00};
const unsigned char *Ico_table[5] = { str_guandan, str_doudizhu, str_tao, str_xin, str_mei };
const unsigned char *Ico_table2[3] = { str_play, str_continue, str_setup };
uint8_t mode_selection = 2;
#endif
//digital analogwrite conflict; compensate is too much; running time count to debug/ remain card to debug, 4 players in endless loop/ 1st card compensation is not enough
//_1_2在连续发牌和随机中，均正常使用了定时器中断更稳定的驱动主轴stepper，并且通过高速低速两个表实现了更快的转速，及更好的卡滞的兼容性。
//随机模式中，想在旋转过程加载及发牌提升效率，但在中断过程中开启和停止直流电机会造成定时器中断混乱，未能在本版本解决。
//PWM驱动DC电机模式在本版本也不成功，soft start直接产生异常，连续低速发牌死循环。
//EEPROM.const uint8_t coesetup[8] PROGMEM = { 108, 0, 4, 32, 0, 255, 1, 1 };

const unsigned int low_speed_table[256] PROGMEM =  //12v 20.8khz 能驱动约800g；8v 17.8k 驱动800g 开始丢步
  { 62500, 8445, 4528, 3094, 2349, 1893, 1586, 1364, 1197, 1066, 961, 875, 803, 742, 689, 644, 604, 569, 537, 509, 484, 461, 440, 421, 404, 388, 373, 359, 346, 334, 323, 313, 303, 294, 285, 277, 270, 262, 255, 249, 243, 237, 231, 226, 221, 216, 211, 207, 202, 198, 194,
    190, 187, 183, 180, 177, 173, 170, 167, 165, 162, 159, 157, 154, 152, 149, 147, 145, 143, 141, 139, 137, 135, 133, 131, 129, 128, 126, 124, 123, 121, 120, 118, 117, 116, 114, 113, 112, 110, 109, 108, 107, 105, 104, 103, 102, 101, 100, 99, 98, 97, 96, 95, 94, 93, 92,
    91, 91, 90, 89, 88, 87, 87, 86, 85, 84, 84, 83, 82, 81, 81, 80, 79, 79, 78, 78, 77, 76, 76, 75, 75, 74, 73, 73, 72, 72, 71, 71, 70, 70, 69, 69, 68, 68, 67, 67, 66, 66, 65, 65, 65, 64, 64, 63, 63, 62, 62, 62, 61, 61, 60, 60, 60, 59, 59, 59, 58, 58, 58, 57, 57, 57, 56, 56,
    56, 55, 55, 55, 54, 54, 54, 53, 53, 53, 53, 52, 52, 52, 51, 51, 51, 51, 50, 50, 50, 50, 49, 49, 49, 49, 48, 48, 48, 48, 47, 47, 47, 47, 46, 46, 46, 46, 46, 45, 45, 45, 45, 44, 44, 44, 44, 44, 43, 43, 43, 43, 43, 42, 42, 42, 42, 42, 42, 41, 41, 41, 41, 41, 41, 40, 40, 40,
    40, 40, 39, 39, 39, 39, 39, 39, 39, 38, 38, 38, 38, 38 };
const unsigned int high_speed_table[256] PROGMEM =  //通过插值更新
  { 38, 38, 38, 38, 37, 37, 37, 37, 37, 37, 37, 37, 37, 37, 36, 36, 36, 36, 36, 36, 36, 36, 36, 36, 36, 35, 35, 35, 35, 35, 35, 35, 35, 35, 35, 35, 35, 34, 34, 34, 34, 34, 34, 34, 34,
    34, 34, 34, 34, 34, 33, 33, 33, 33, 33, 33, 33, 33, 33, 33, 33, 33, 33, 33, 32, 32, 32, 32, 32, 32, 32, 32, 32, 32, 32, 32, 32, 32, 32, 32, 31, 31, 31, 31, 31, 31, 31, 31, 31, 31, 31,
    31, 31, 31, 31, 31, 31, 30, 30, 30, 30, 30, 30, 30, 30, 30, 30, 30, 30, 30, 30, 30, 30, 30, 30, 30, 29, 29, 29, 29, 29, 29, 29, 29, 29, 29, 29, 29, 29, 29, 29, 29, 29, 29, 29, 29, 29,
    28, 28, 28, 28, 28, 28, 28, 28, 28, 28, 28, 28, 28, 28, 28, 28, 28, 28, 28, 28, 28, 28, 28, 27, 27, 27, 27, 27, 27, 27, 27, 27, 27, 27, 27, 27, 27, 27, 27, 27, 27, 27, 27, 27, 27, 27,
    27, 27, 27, 26, 26, 26, 26, 26, 26, 26, 26, 26, 26, 26, 26, 26, 26, 26, 26, 26, 26, 26, 26, 26, 26, 26, 26, 26, 26, 26, 26, 26, 25, 25, 25, 25, 25, 25, 25, 25, 25, 25, 25, 25, 25, 25,
    25, 25, 25, 25, 25, 25, 25, 25, 25, 25, 25, 25, 25, 25, 25, 25, 25, 25, 24, 24, 24, 24, 24, 24, 24, 24, 24 };


typedef struct
{
  unsigned char index;
  unsigned char up;
  unsigned char down;
  unsigned char back;
  unsigned char forward;
  void (*operation)(void);
} KEY_TABLE;

unsigned char funIndex = 0;
void (*current)(void);
void menu_1(void);
void menu_2(void);
void menu_running(void);
void menu_setup(void);
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
void loop() {
  // put your main code here, to run repeatedly:
  if (mode_type == mode_1by1) {
    firstcard();
    ;
    while (mode_type == mode_1by1) {
      while (check_point == 0)
        ;
      card_shoot();
      check_point = 0;
      if (startover) { break; }
    }
    mode_type = 0;
  } else if (mode_type == mode_random) {
    random_mode();
  } else if (startover) {
    startover = 0;
    delay(500);
  }
#ifdef ble_enable
  else if (Serial.available() > 0) {
    modeset();
    if (startover) { return; }
  }
#endif
#ifdef screen_enable
  ButtonCheck();
#endif
}

void batcheck() {
  bat = analogRead(volread);
  if (bat > 470) {
    bat = 470;
  } else if (bat < 330) {
    bat = 330;
  }
  bat = bat - 330;
  bat = map(bat, 0, 140, 0, 4);
  /*
byte bat1;
if (bt==1023) {Serial.println("FC20");return;} //99 stand for failure, 002 MCU REF V is grounded
else if (bt>870){Serial.println("FC21");return;} //99 stand for failure, 001 bat is over charged  *0.5055 ceo stand for 8.5v
else if (bt<650){Serial.println("FC22");return;}//99 stand for failure, 000 bat is low stand for 6.5v, measurement result 686 indicate6.5v 
else if (bt>850){bt=850; bt=bt-650; bat1=map(bt,0,200,0,100);} //bt*5/1023/0.5055=real / 4.2/real *255  (105494-4v)
else {bt=bt-650; bat1=map(bt,0,200,0,100);}
if (bat1<bat){bat=bat1;}*/
}

void FC_print(byte i) {
#ifdef ble_enable
  switch (i) {
    case 0:
      stoprun();
      startover = 1;
      Serial.println((String) "FC00" + (holdcards + totalcards - cardout) + "CARDS MISSING");  //FC00:SOCKET EMPTY
      break;
    case 1:
      stoprun();
      startover = 1;
      Serial.println((String) "FC01 REMAIN CARDS=" + (holdcards + totalcards - cardout));  //FC01: LOAD FAILED
      break;
    case 2:
      stoprun();
      startover = 1;
      Serial.println((String) "FC02 REMAIN CARDS=" + (holdcards + totalcards - cardout));  //FC02:SHOOT TIMEOUT
      break;
    case 5:
      startover = 0;
      flashing(600, 200, 2);
      Serial.println((String) "Mod" + mode_type + " Cd" + totalcards + " H=" + holdcards + " P=" + players + " Spd" + maxfqy + " Bat=" + bat + " SW" + SW_V);
      break;
    case 4:
      stoprun();
      Serial.println((String) "FC04");  //FC04:TOO MUCH LOAD STUCK
      break;
    case 6:
      t_total = millis() - t_start;
      stoprun();
      flashing(500, 500, 3);
      Serial.println((String) "Set In" + t_total + "ms, Enjoy");
      break;
    case 10:
      startover = 1;
      Serial.println("FC10");  //FC10:It's not a valid command/improper setup
      break;
  }
#endif
#ifdef screen_enable
  stoprun();
  startover = 1;
  display.clearDisplay();
  switch (i) {
    case 0:
      display.setCursor(15, 24);
      display.println(F("FC00"));
      break;  //display.setCursor(5, 24);display.println(string(holdcards + totalcards - cardout));display.setCursor(45, 24);display.println(F("MISSING"));
    case 1:
      display.setCursor(15, 24);
      display.println(F("FC01"));
      break;
    case 2:
      display.setCursor(15, 24);
      display.println(F("FC02"));
      break;
    case 6:
      display.setCursor(15, 24);
      display.println(F("ENJOY!"));
      break;
    default: break;
  }
  display.display();
#endif
}

void ButtonCheck() {
  while (1) {
    if (digitalRead(touchpad1)) {
      //Serial.println("Button1 On");
      button_on = 0;  //up
      touchcounting(touchpad1);
      break;
    }
    if (digitalRead(touchpad2)) {
      //Serial.println("Button2 On");
      button_on = 2;  //down
      touchcounting(touchpad2);
      break;
    }
    if (digitalRead(touchpad3)) {
      //Serial.println("Button3 On");
      button_on = 3;
      touchcounting(touchpad3);
      break;
    }
    if (digitalRead(touchpad4)) {
      //Serial.println("Button4 On");
      button_on = 1;  //gogo
      touchcounting(touchpad4);
      break;
    }
    delay(10);
  }
}

//touch measurement to use "touchcounting"
void touchcounting(uint8_t j) {
  uint16_t i = 0;
  uint8_t k = 0;
  uint8_t touch_threshold = 150;  //intially 1s, dynamic control, in case keeping touch, this number will be smaller and smaller therefore the touchcounting will be faster
  while (digitalRead(j)) {
    delay(2);
    i++;
    if (i > touch_threshold) {
      touchevent(button_on);  //no accumulated touch count, each time reaches the threshold
      i = 0;
      if (touch_threshold < 20) {
        touch_threshold = 20;
      } else {
        k++;
        if (touch_threshold > 20) {
          touch_threshold = touch_threshold - k * k;
        }
      }
    }
  }
}

void touchevent(uint8_t i) {

  switch (i)  //获取按键对应序号
  {
    case 1:
      setup_save(funIndex);
      funIndex = menu[funIndex].forward;
      break;
    case 3: funIndex = menu[funIndex].back; break;
    case 2: funIndex = menu[funIndex].down; break;
    case 0: funIndex = menu[funIndex].up; break;
  }
  current = menu[funIndex].operation;  //根据需要获取对应需要执行的函数
  (*current)();                        //执行获取到的函数
}

void setup_save(int i) {
  if (funIndex < 5) {
    switch (i) {
      case 0:
        totalcards = 108;
        holdcards = 0;
        players = 4;
        maxfqy = 30;
        break;
      case 1:
        totalcards = 54;
        holdcards = 3;
        players = 3;
        maxfqy = 30;
        break;
      case 2:
        totalcards = 54;
        holdcards = 0;
        players = 3;
        maxfqy = 30;
        break;
      case 3:
        totalcards = 108;
        holdcards = 8;
        players = 4;
        maxfqy = 80;
        break;
      case 4:
        totalcards = 52;
        holdcards = 0;
        players = 4;
        maxfqy = 36;
        break;
    }
    speed_table_lookup();
    loopstep = basestep / players;
    slip_step = loopstep - (high_accel_step + low_accel_step);  // slip until that step, not pure slip step
    motorspeed = 255;
    fast_break = 1;
  } else if (funIndex == 5) {
    goon = 0;
    cardout = 0;
    mode_type = mode_selection;
  } else if (funIndex == 6) {
    goon = 1;
    mode_type = mode_selection;
  } else if (funIndex == 9) {
    mode_selection = mode_random;
  } else if (funIndex == 10) {
    mode_selection = mode_1by1;
  }
}

void menu_1() {  //mode selection
  display.clearDisplay();
  display.drawBitmap(56 + 40 * (button_on - 1), 21, Ico_table[funIndex], 40, 40, 1);
  display.drawBitmap(56 - 40 * (button_on - 1), 21, Ico_table[((funIndex + 4 - button_on) % 5)], 40, 40, 1);
  draw_bat();
  display.display();
  delay(100);
  display.clearDisplay();
  display.drawBitmap(44, 21, Ico_table[funIndex], 40, 40, 1);
  display.drawBitmap(-20, 21, Ico_table[((funIndex + 4) % 5)], 40, 40, 1);
  display.drawBitmap(108, 21, Ico_table[((funIndex + 1) % 5)], 40, 40, 1);
  draw_bat();
  switch (funIndex) {
    case 0:
      display.setCursor(0, 0);
      display.println(F("GUANDAN"));
      break;
    case 1:
      display.setCursor(0, 0);
      display.println(F("DOUDIZHU"));
      break;
    case 2:
      display.setCursor(0, 0);
      display.println(F("BLACK5"));
      break;
    case 3:
      display.setCursor(0, 0);
      display.println(F("FREEMODE1"));
      break;
    case 4:
      display.setCursor(0, 0);
      display.println(F("FREEMODE2"));
      break;
  }
  display.display();
}

void menu_2() {  //action selection
  display.clearDisplay();
  display.drawBitmap(56 + 40 * (button_on - 1), 21, Ico_table2[(funIndex - 5)], 40, 40, 1);
  display.drawBitmap(56 - 40 * (button_on - 1), 21, Ico_table2[((funIndex - 3 - button_on) % 3)], 40, 40, 1);
  draw_bat();
  display.display();
  delay(100);
  display.clearDisplay();
  display.drawBitmap(44, 21, Ico_table2[(funIndex - 5)], 40, 40, 1);
  display.drawBitmap(-20, 21, Ico_table2[((funIndex - 3) % 3)], 40, 40, 1);
  display.drawBitmap(108, 21, Ico_table2[((funIndex - 4) % 3)], 40, 40, 1);
  draw_bat();
  switch (funIndex) {
    case 5:
      display.setCursor(1, 1);
      display.println(F("RUN"));
      break;
    case 6:
      display.setCursor(1, 1);
      display.println(F("CONTINUE"));
      break;
    case 7:
      display.setCursor(1, 1);
      display.println(F("SETUP"));
      break;
  }
  display.display();
}

void draw_bat() {
  batcheck();
  //display.setCursor(96, 0);display.println(bat);
  display.drawRect(111, 2, 15, 8, 1);  //outline
  if (bat > 0) {
    for (byte i = 0; i < bat; i++) { display.fillRect(113 + i * 3, 4, 2, 4, 1); }
  }
  display.drawLine(126, 5, 126, 7, 1);
}

void menu_running() {
  display.clearDisplay();
  display.setCursor(15, 24);
  display.println(F("RUNNING"));
  //draw_bat();
  display.display();
}
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

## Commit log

2024-05-26 Add files via upload
    PCB file
2024-07-31 Update smart_poker_dealer_v0.ino
    bug fix_long shooting overtime was skipping some ISR event
    [smart_poker_dealer_v0.ino]
2024-08-11 Add files via upload
    PCB for V2
